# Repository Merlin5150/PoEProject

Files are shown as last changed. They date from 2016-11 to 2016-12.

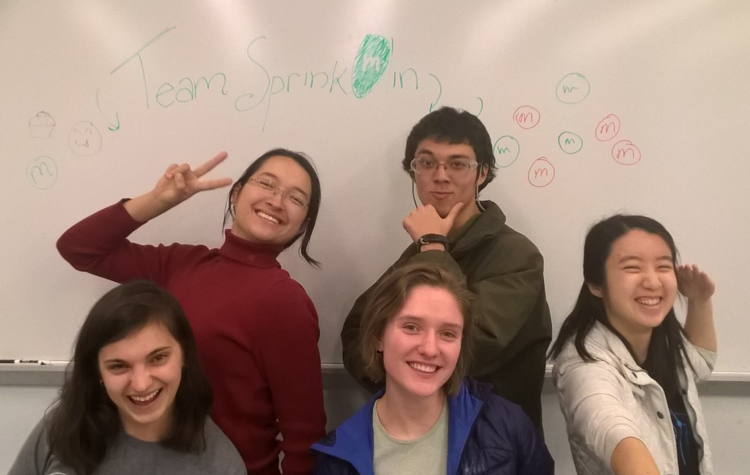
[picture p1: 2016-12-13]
images/team.png

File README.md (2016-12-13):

# CNC M&M printer
## Team SprinkOlin | Principles of Engineering Fall 2016
Behold! The machine that takes an image and a pastry and faithfully recreates said image on said pastry with the aid of a computer program, a two-axis gantry, and a dispenser system. The result? A tasty-looking, creative picture.

In more words: the CNC M&M printer is a 2-axis gantry attached to a dispenser that interprets image-processing and movement code from an arduino to replicate a user inputted picture. First, the image processing code interprets the user's image makes it into "mixels" or MnM-sized pixels. Then the movement-related code translates the sprixel pattern into a series of movements and communicates them to the gantry. The dispenser on the rods of the gantry is moved by a series of belts along rods, pausing occasionally to release an M&M onto the icing-coated surface beneath it. This icing-coated surface's height can be adjusted by moving the build plate up and down teeth on the comb-like structures on which it rests.

This repo contains code for image processsing and serial transmission of insructions over serial to an Ardunio in Python, [serialWriting.py](https://github.com/kuannie1/PoEProject/blob/master/serialWriting.py), and code in Arduino C to recieve instructions and move the gantry accordingly, [StepperControl.ino](https://github.com/kuannie1/PoEProject/blob/master/Arduino/StepperControl/StepperControl.ino). 

This project was created as a final project for the Principles of Engineering course at [Olin College of Engineering](olin.edu). 
### Subsystems
#### Mechanical System

The gantry is a 2-axis gantry composed of rods held up by rail-shaft guide supports screwed into the a lasercut hardboard structure. Stepper-motor controlled gears across from pulleys are aligned with both axes. The gears and pulleys hold thin rubber belts that are moved by the stepper-controlled gears. The stepper motors themselves sit on tiny platforms in the corners of the gantry. The belt on the on the front-back axis attaches to a hardboard structure encasing the gear on the end of the left-right pair of rods. The belt on the left-right axis attaches to the dispenser structure. The entire left-right axis including the dispenser moves along the front-back axis with the help of linear bearings embedded in the hardboard structures at the end of the left-right axis. Similarly, the dispenser uses two linear bearings in its hardboard structure to move along the left-right axis. The build plate beneath the entire structure moves up and down depending on what notches on four comb-like devices the build plate is placed on.

The dispenser itself is entirely 3D printed. It consists of two tubes attached to the dispenser itself, which then attaches to the hardboard piece that moves along the left-right axis. The top tube is wide enough to loosely fit an MnM, which was established to help prevent jamming, and is tall enough to hold many vertically stacked MnMs at a time. The dispenser itself includes a cylinder with a circular cup-shaped divot spun by a mini servo motor inside of a structure that holds it between the top tube. The bottom tube, which is the same diameter as the top, but reaches down about half an inch above the build plate. The bottom tube also attaches to the hardboard piece moving along the left-right axis via a small rectangle that fits around the structure. The structure that holds the tubes above and below the dispenser also includes a small shield to prevent MnMs from falling forward while the cylinder is turning. The MnM drops down the top tube into the cup on the cylinder, which is then turned in such a way that it drops down into the bottom tube and lands on the build plate.

#### Software System

The image processing software as written in Python. It utilizes the OpenCV packages to process user-inputted images and convert them to stepper motor commands. The software takes in some black and white image, and resizes it to a 30 by 30 pixel matrix before identifying each pixel’s color. It then converts the color information into a series of motor commands, telling the gantry motors when and how far to move the dispenser. This information is sent through the serial stream to provide commands to the firmware.

#### Firmware System

Using the signals from the software's input from serial, the Arduino Uno and Sparkfun Motor Sheild uses Arduino C to convert those commands to determine which coils within the stepper motor should be magnetized. Those commands also indicate when to turn the servo motor in the dispenser. When the gantry stepper motors translate the dispenser to the next destination, the servo motor on the dispenser receives the command to turn and dispense an M&M.

#### Electrical System

The electrical system ensures that everything in the system is working smoothly. The limit switches mounted on the gantry help the steppers keep track of the dispenser's location and calibrates the motors if needed. In addition to the limit switches, the stepper motors and servos are connected to the firmware through jumper wires for secure connections.

### Build it Yourself!
1. The list of materials that we used for prototyping and our final build can be found [here](https://docs.google.com/spreadsheets/d/1XF6dD36GEhaLRRnJzzlNKo4jniRV8MezCQr9N6U7E4w/edit?usp=sharing.
2. Download the full CAD from [GrabCAD](https://grabcad.com/library/cnc-m-m-placer-2).
3. Laser cut the part files found in "_to_cut_.zip". For our project, we used the [Epilog Helix Laser Cutter](https://www.epiloglaser.com/index.htm). Most of these parts can also be cut by hand, although more labor may be needed to achieve the same quality.
4. Assemble the frame of the gantry based on the CAD and included drawings.
5. Put the build plate on a level uniform across the four comb structures.
6. Attach the rail-shaft guide supports with screws to the tops of each corner of the frame on the outside.
7. Assemble the hard board pieces associated with the left-right axis. Put linear bearings in the large holes on the outsides of these structures.
8. Run the forward-backward rods through these linear bearings.
9. Then run the rods through the rail-shaft guide supports and screw screws into the top holes of each rail shaft guide support to secure the rods.
10. Attach rail-shaft guide supports on the outsides of the bottom pieces of the hardboard pieces that are now sitting on the forward-backward axes. Screw them in as shown.
11. Assemble the middle hardboard piece shown to be attached to the left-right axis. Put linear bearings in the larger holes toward the bottom of this piece.
12. Run the left-right rods through the rail-shaft guide supports through the outside hardboard component on one side of the left-right axis, then through the linear bearings on the center piece, and then through the linear bearings on the hardboard component on the other side of the left-right axis. Tighten screws on the ends of the rail-shaft guide supports to secure the rods.
13. 3D print the dispenser and file as needed. Carefully hot-glue the top tube to the tube-shaped part of the dispenser. Then fit the bottom of the dispenser piece onto the bottom tube. Place the square-shaped attachment piece along the center part of the hardboard on the left-right axis. Glue this piece down as needed. Attach the mini servo to the small bead-shaped attachment poking out to the left side.
14. Secure the belts along the pulleys and gears by cutting them and attaching them around these components and to small slots on the end of the corresponding hardboard pieces. Small zipties are very useful in case the holes are too big or the belt is long enough to fit through both holes and meet in the middle.
15. Re-create the electrical systems as demonstrated by the electrical diagrams. Attach the limit switches on the front-right side of the forward-back axis and on the side of the center hardboard piece of the left-right axis facing the axis with the other limit switch on it.
16. The circuit can be recreated from the diagram [circuitDiagram_schem](https://github.com/kuannie1/PoEProject/blob/master/circuitdiagram/circuitDiagram_schem.pdf). We soldered our wires to a protoboard and added jumper connections for easy customizability, but a simple breadboard and jumper set up will work just fine!
17. Solder wires to the limit switches according to the diagram
18. Screw wires into the barrel jack connectors to make the adaptor cable. This will plug into the motor shield
19. Assemble circuit on a breadboard or protoboard and plug jumpers into appropriate Arduino pins.
20. Download the Arduino code and Python code, adjust parmeters for your gantry geometry, and you are ready to go!
21. To run, first upload the Arduino code, and then run the python script from the terminal.

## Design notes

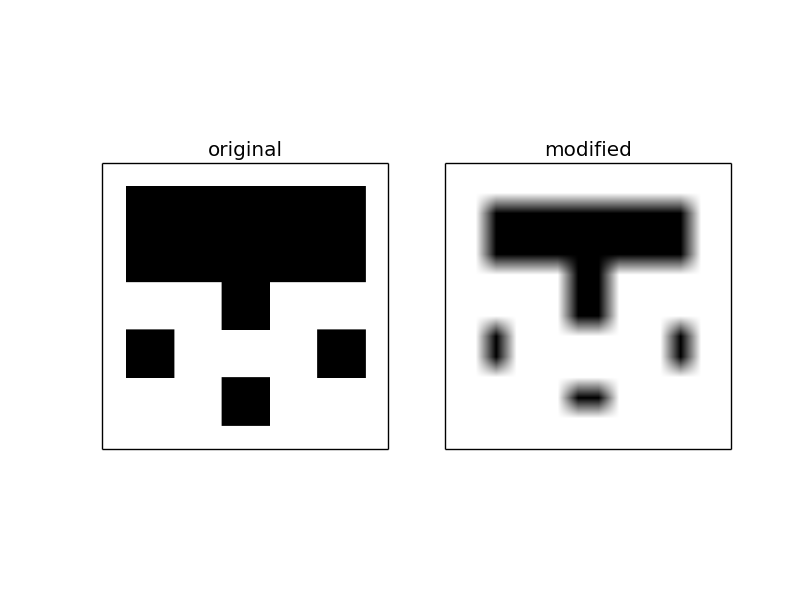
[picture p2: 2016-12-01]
comparisonfigures/comparison_figure_4.png

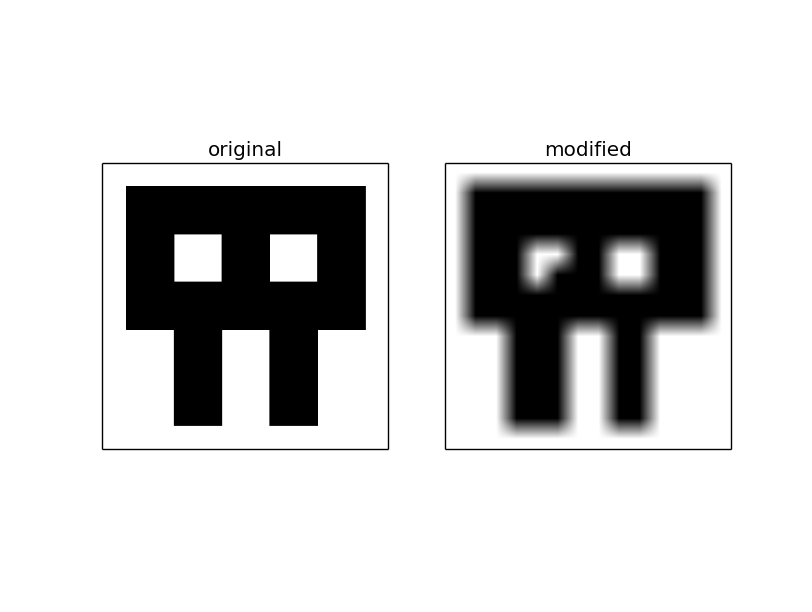
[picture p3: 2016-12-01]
comparisonfigures/comparison_figure_2.png

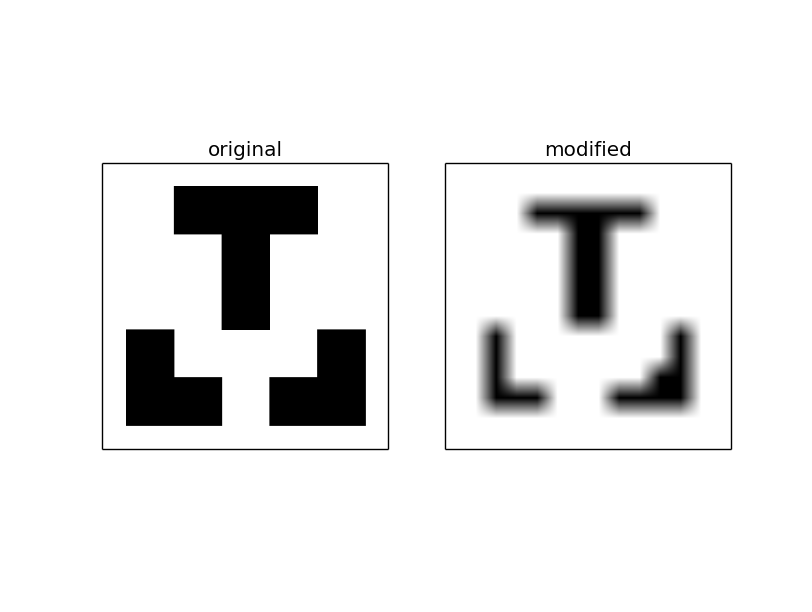
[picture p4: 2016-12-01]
comparisonfigures/comparison_figure_1.png

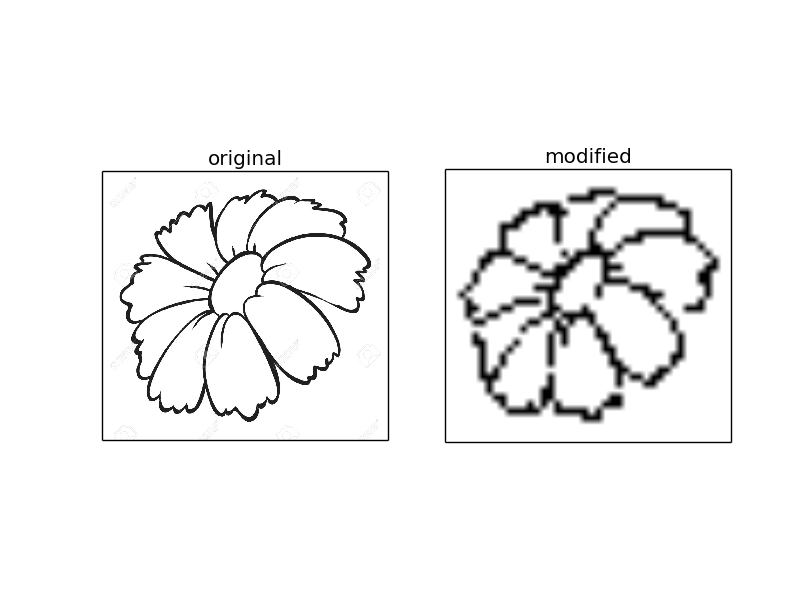
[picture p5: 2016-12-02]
comparisonfigures/comparison_flower.png

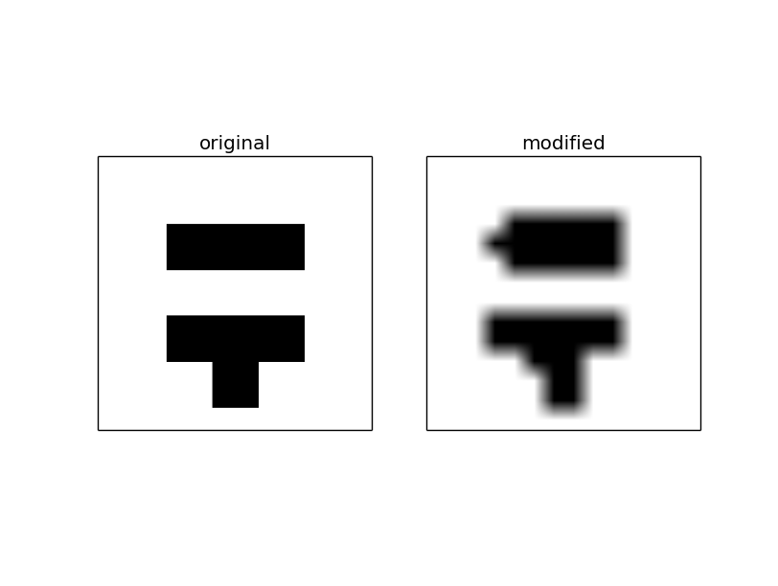
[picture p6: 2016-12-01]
comparisonfigures/comparison_figure_3.png

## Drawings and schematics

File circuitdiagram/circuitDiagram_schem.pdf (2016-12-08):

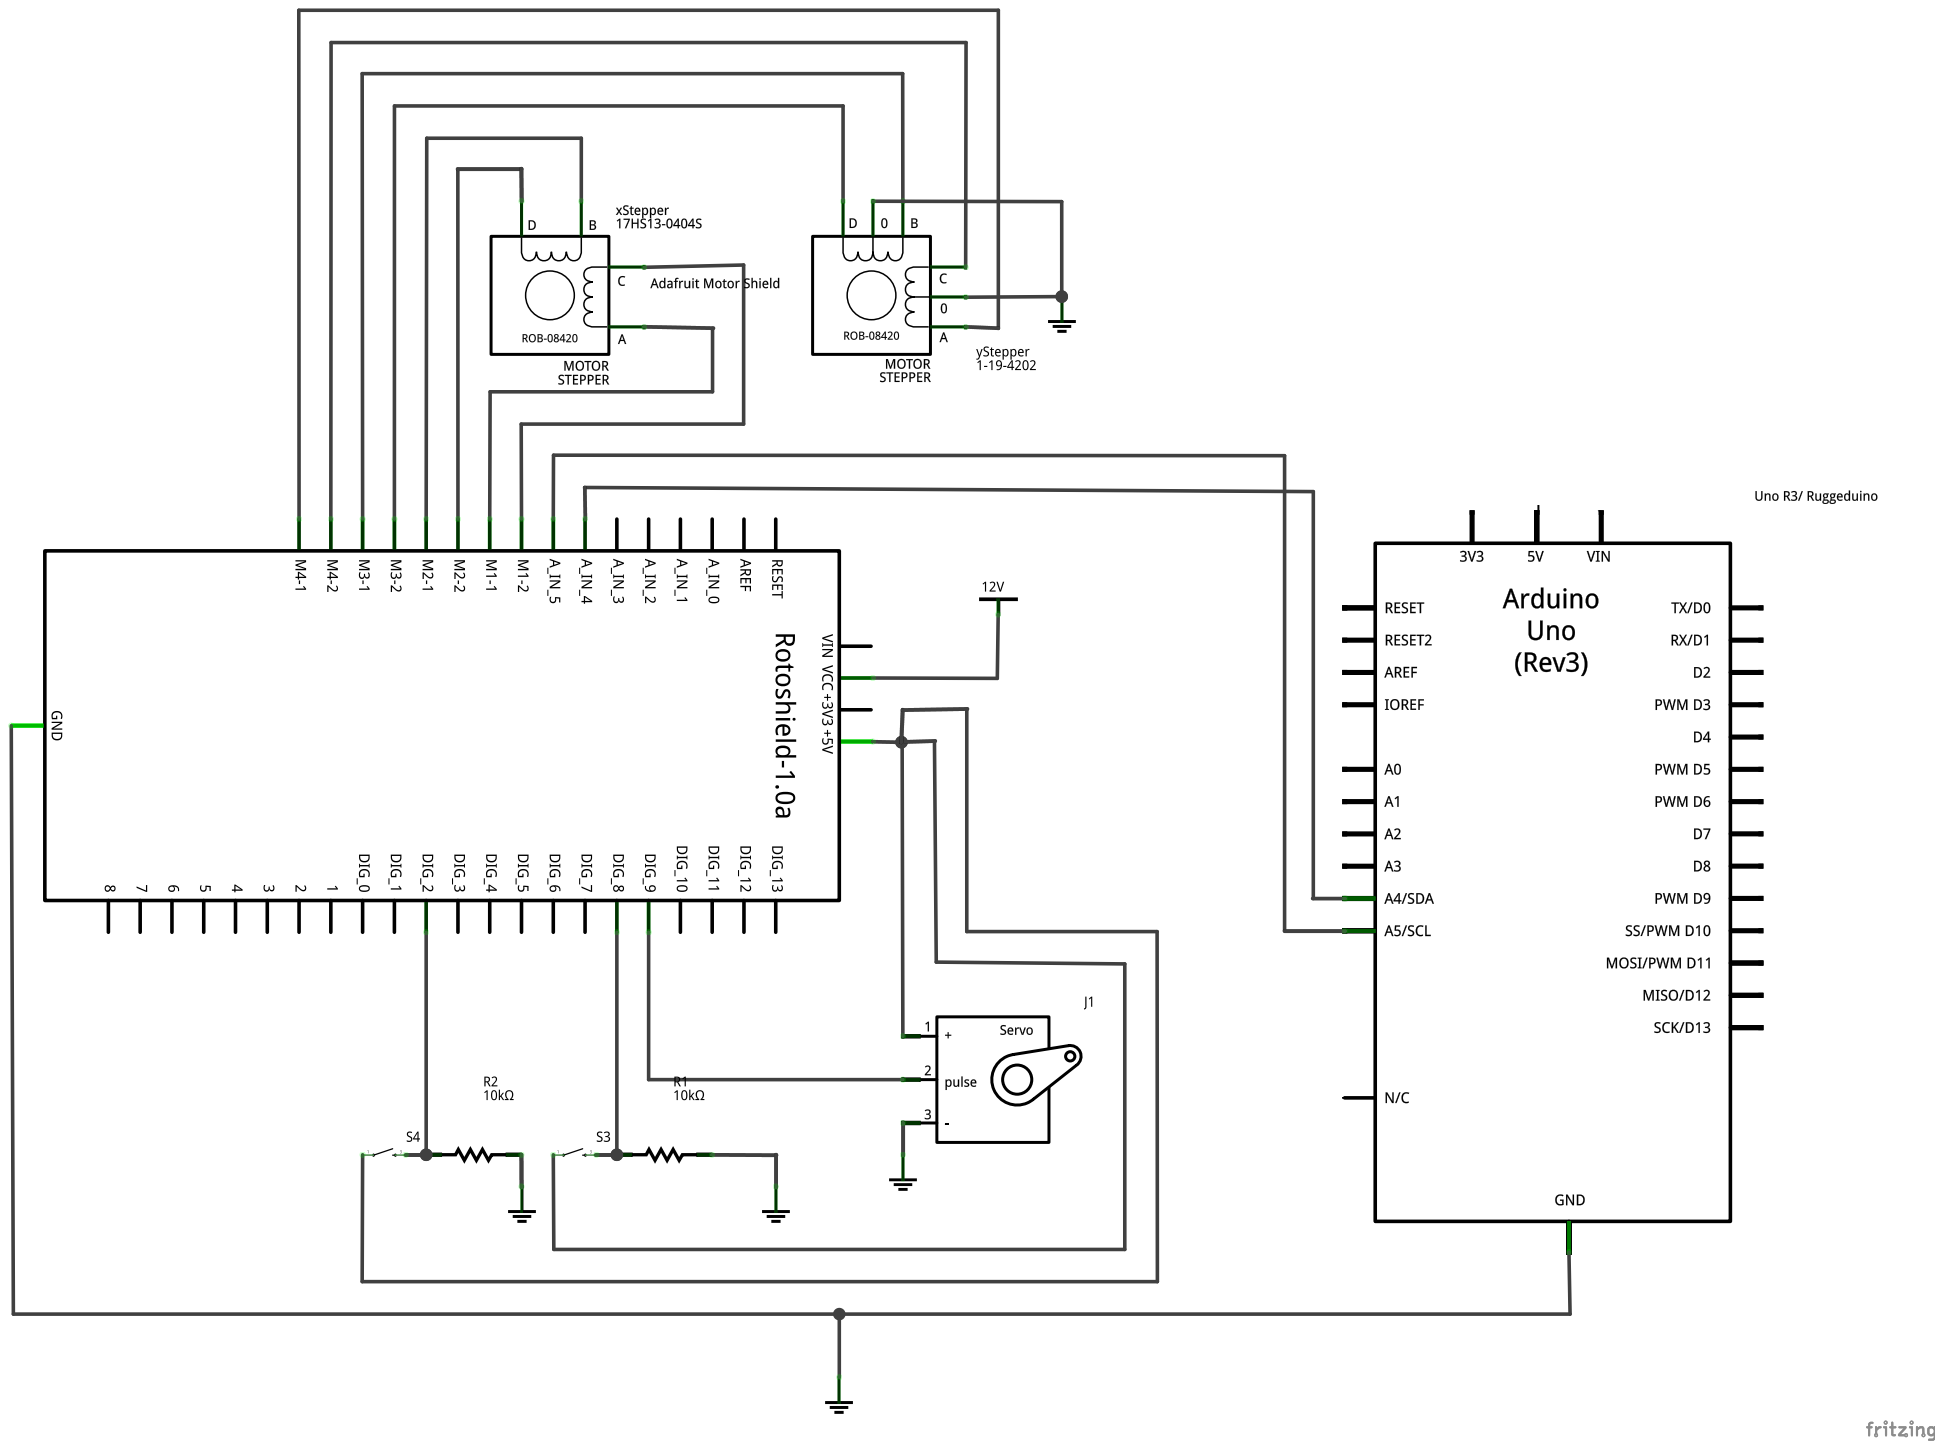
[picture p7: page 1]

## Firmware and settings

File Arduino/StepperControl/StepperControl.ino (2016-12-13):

/*
  Poe Project 2016: CNC M&M Printer

  Receives commands via serial
  Controls the steppers that move the gantry using the Adafruit Motor 
  Controls the dispensing system
  For use with 2 axis gantry

  Instructions are written to serial in the form: "<direction stepperX><displacement stepperX><direction stepperY><displacement stepperY>"
  in which 0 represents BACKWARDS and 1 represents FORWARDS

  by Team SprinkOlin
*/

#include <Adafruit_MotorShield.h>
#include <Servo.h>

Adafruit_MotorShield AFMSbot(0x60);

// Connect stepper motors with 200 steps per revolution (1.8 degrees per step)
// to the motorports on the shield

// the gantry steppers:
Adafruit_StepperMotor *xStepper = AFMSbot.getStepper(200, 1); // M1 and M2
Adafruit_StepperMotor *yStepper = AFMSbot.getStepper(200, 2); // M3 and M4


// initialize Servo Motor object
Servo sprinkleServo;  // for the agitator in the hopper

// limit switch pins
const int switch1 = 8;  // corresponds to xStepper
const int switch2 = 2;  // corresponds to yStepper 

const int servoPin = 9;  // the agitator servo pin

// flags to determine callibration status
// these are passed as arguments into the callibration function (defined below)
int stop1 = false;  // corresponds to xStepper  
int stop2 = false;  // corresponds to yStepper

// initialize command variables. These will be used to store the desired number of steps
// that the motors are commanded to go (command obtained via Serial)
int stepCommandX = 0;
int stepCommandY = 0;

// setting min and max positions ensures that the steppers do not rotate past the limits of the gantry
// these are experimentally determined and may vary greatly depending on gantry geometry
int maxPositionX = 710;
int minPositionX = 0; 
int maxPositionY = 2100;
int minPositionY = 0;

// Because steppers, unlike servos, cannot keep track of their position, we need
// to keep track of the positions relative to the zero position (obtained by calibration)
// The initial positions are set to zero and are updated as the motors read commands 
// from Serial 
int stepperPositionX = 0;
int stepperPositionY = 0;

void calibrate(Adafruit_StepperMotor* motor, int switchPin, bool flag) {
  // Runs the motor towards the home position, until it hits a limit switch, indicating that the
  // motor should stop running.
  // motor: a pointer to a motor object. Either xStepper or yStepper in this code.
  // switchPin: the pin of the limit switch corresponding to motor.
  // flag: indicator whether switch was press. Either stop1 or stop2 in this code.
  
  while (flag == false) {
    // run the motor towards the home position until the button is pressed
    int buttonState = digitalRead(switchPin);
    if (buttonState == HIGH) {
      flag = true;
      break;
    }
    motor->step(1, BACKWARD, INTERLEAVE);
    delay(3);
  }
  motor->step(100, FORWARD, INTERLEAVE); // steps away from the limit switch to position dispenser over gantry
}

int moveMotor(Adafruit_StepperMotor* motor, int stepCommand, int stepperPosition, int minPosition, int maxPosition) {
  // processes instructions into motor movement. 
  // motor: a pointer to a motor object. Either xStepper or yStepper in this code.
  // stepCommand: desired number of steps the motor should rotate. Negative
  // command denotes a backwards rotation.
  // stepperPosition: the current position of the motor
  // minPosition: minimum coordinate the stepper can move the dispenser to
  // maxPosition: maximum coordinate the stepper can move the dispenser to
  
    // handles positions outside of the limits of the gantry geometry
    if (stepperPosition + stepCommand < minPosition) { //Before minPositionX was 0
      // limits number of steps to above the minimum position (defined as 0)
      // only goes as many steps as possibe before minimum position is reached
      motor->step(abs(minPosition - stepperPosition), BACKWARD, INTERLEAVE);
      stepperPosition = 0;
    }

    else if (stepperPosition + stepCommand > maxPosition) {
      // limits number of steps to below the maximum position
      // only goes as many steps as possible before maximum is reached
      motor->step(maxPosition - stepperPosition, FORWARD, INTERLEAVE);
      stepperPosition = maxPosition;
    }

    else {
      // if the stepper is within the upper and lower limits, it can move noramlly
      if (stepCommand > 0) {
        // move the stepper in the positive direction
        motor->step(stepCommand, FORWARD, INTERLEAVE);
        delay(3);
      }

      else {
        // move the stepper in the negative direction
        motor->step(abs(stepCommand), BACKWARD, INTERLEAVE);
        delay(3);
      }
      stepperPosition += stepCommand;
    }
    return stepperPosition; // this is used to update the position of the motor
}

void setup() {
  // initialize the button pin as an input:
  pinMode(switch1, INPUT);
  pinMode(switch2, INPUT);

  // attach servo object and set to starting position
  sprinkleServo.attach(servoPin);
  sprinkleServo.write(179);

  Serial.begin(9600);

  // allows us to communicate with the motor shields with I2C
  AFMSbot.begin();

  // set the stepper speeds
  xStepper->setSpeed(50);  // 50 rpm
  yStepper->setSpeed(50);

  // run the calibration sequence on the motors
  calibrate(xStepper, switch1, stop1);
  calibrate(yStepper, switch2, stop2);
  delay(100);
  Serial.flush(); // clears the serial buffer
  Serial.println("Ready");
}

void loop() {
  // In order to not get strange readings from serial, we want to make sure that
  // all 4 bytes needed to create a complete command sequence are available before reading from Serial
  if (Serial.available() >= 4) {
    
    // Because characters are 1 byte and ints are 4 bytes, we have to be careful to cast our Serial
    // readings to a character to ensure that the right information is being communicated!'

    // read direction command for xStepper
    char signX = (char)Serial.read();

    // read displacement of xStepper, scale to accomodate size of M&M
    int stepCommandX = 75 * (int)(char)(Serial.read());
      if (signX == 0) {
        stepCommandX *= -1; // negates the desired number of steps to indicate motor should rotate backwards
      }

    // read direction command for yStepper
    char signY = (char)Serial.read();

    // read displacement of xStepper, scale to accomodate size of M&M
    // we scaled this command by an extra factor of 2 because the step size of ystepper was half that of xStepper
    int stepCommandY = 75 * 2 * (int)(char)Serial.read();
      if (signY == 0) {
        stepCommandY *= -1; // negates the desired number of steps to indicate motor should rotate backwards
      }


    stepperPositionX = moveMotor(xStepper, stepCommandX, stepperPositionX, minPositionX, maxPositionX);  
    stepperPositionY = moveMotor(yStepper, stepCommandY, stepperPositionY, minPositionY, maxPositionY); 
    delay(1000); // large delay to allow time for motors to move
    

    // turn the dispenser to dump an m&m
    sprinkleServo.write(1);
    delay(500);
    sprinkleServo.write(179);
    delay(500);
  }
}

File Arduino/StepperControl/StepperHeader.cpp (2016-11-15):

class StepperMotor {
private:

	Adafruit_StepperMotor * motor;

	int minPosition
	int maxPosition;
	int position;

public:

	StepperMotor(Adafruit_StepperMotor * motor, int minPosition, int maxPosition) {
		
		this->minPosition = minPosition;
		this->maxPosition = maxPosition;

		// initialize position
		this->position = 0;
	}

	void Update(int stepCommand) {
		position += stepCommand;

		if (position > maxPosition) {
			// limits number of steps to below the maximum position
        	// only goes as many steps as possible before maximum is reached
			motor->step(position - maxPosition, FORWARD, INTERLEAVE);
			position = maxPosition;
			delay(3);
		}

		else if (position < 0) {
			motor->step(position - stepCommand, BACKWARD, INTERLEAVE);
			position = 0;
			delay(3);
		}

		else {
			if (stepCommand > 0) {
				motor->step(stepCommand, FORWARD, INTERLEAVE);
				delay(3);
			}

			else {
				motor->step(stepCommand, BACKWARD, INTERLEAVE);
				delay(3);
			}
		}

	}

}

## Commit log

2016-10-18 for stepper control using Adafruit Motor Shield
2016-10-26 can enter an integer of any size into serial without weird ascii conversions. Stepper only moves within the bounds speciified. Ability to easily return stepper to 0 position
2016-10-28 testing image print
2016-10-28 Updated Arduino motor code
2016-11-04 custom library for adding steppers
2016-11-07 playing with adding motor arguments to functions
2016-11-08 fixed code; commented for readability
    [serialWriting.py]
2016-11-08 added in a servo
2016-11-10 updated servo portion
2016-11-11 changed the servo angle and fixed the action order
    [StepperControl.ino]
2016-11-13 fixed a spelling mistake
    [StepperControl.ino]
2016-11-15 added variables for 2nd stepper
2016-11-15 starting header file for motor management
2016-11-15 added capability for another motor and changed serial communication slightly
2016-11-17 added limit switches, calibration, dispenser stepper
2016-11-17 playing with sending message to Arduino, not working yet
    [serialWriting.py]
2016-11-29 got serial commands using characters running, added ability to control x and y steppers
2016-12-01 did some image manipulation, pretty set for motor code
2016-12-06 limit switches stop motors when HIGH instead of LOW
2016-12-06 fixed some bugs in the moveMotor function, and updated max step sizes to reflect gantry geometry
    [StepperControl.ino]
2016-12-06 initial commit. circuit diagram of project
    [circuitDiagram.fzz]
2016-12-07 circuit diagram including motors and switches
    [circuitDiagram.fzz]
2016-12-08 obtained gantry coordinates
2016-12-08 allowed error messages regarding chr to pop up
    [serialWriting.py]
2016-12-09 correctly reads instructions from serial
    [StepperControl.ino]
2016-12-13 moved into folder
    [circuitDiagram.fzz]
2016-12-13 moved to appropriate folders
    [circuitDiagram.fzz]
